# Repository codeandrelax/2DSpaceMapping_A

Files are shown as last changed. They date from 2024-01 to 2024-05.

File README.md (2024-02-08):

# O projektu 🚗
Specifikacija projektnog zadatka od strane project owner-a (uopšteni zahtjevi):

- autonomno vozilo
- upravljačka ploča (MCU: PIC24FJ64GAxx)
- lidar
- aplikacija

Cilj projektnog zadatka jeste realizacija autonomnog vozila koje ima mogućnost kretanja kroz prostoriju i mapiranje područja oko njega. Vozilo se sastoji od šasije sa 4 točka (2 slobodna točka i 2 točka pogonjena na DC motor) kojima upravlja upravljačka ploča bazirana na mikrokontroleru PIC24FJ64GA.

Kao ključni element same ploče, koristimo mikrokontroler iz familije PIC24FJ64GA za upravljanje i kontrolu sistema. Za komunikaciju sa već postojećom pločom koristimo I2C, a za komunikaciju sa drugim periferijama koristimo UART i SPI. Jedan od glavnih zahtjeva korisnika jeste da se ostvari bežična komunikacija i daljinsko upravljanje samog vozila, za šta je neophodno koristiti WiFi modul koji povezujemo putem UART interfejsa sa mikrokontrolerom. Mapiranje prostora i kontrola kretanja se vrši uz pomoć Lidara. Korisnik može kontrolisati kretanje vozila pomoću korisničke aplikacije i njenog GUI-a dok prati pogled na prostor u realnom vremenu. Na kraju, neophodno je razviti PC aolikaciju za prikaz reljefa oko samog vozila. Minimalni uslovi koji moraju biti ispunjeni su mogućnost pokretanja i zaustavljanja vozila.
Nakon prvog sastanka sa project owner-om, dobili smo detaljnije specifikacije samog projektnog zadatka koje podrazumijevaju sljedeće:

- PCB pločica može da bude jednoslojna ili dvoslojna
- prilikom izrade PCB ploče koristimo SMD komponente, gdje je to moguće
- minimalna širina veze prilikom rutiranja iznosi 0.254 mm
- nije potrebno projektovati dodatno napajanje, dovoljno je koristiti već postojeće
- budžet za narudzbu i kupovinu komponenata ne bi trebalo da prelazi 30 dolara

Početna šema, neophodna za izradu i projektovanje štampane ploče prikazana je na slici ispod, a detaljnije objašnjenje same šeme i načina spajanja iste nalazi se na Wiki stranici.



Nakon projektovane šema, kao rezultat dobijamo PCB i rutiranu pločicu, prikzanu na slici ispod :



Dostavljamo i 3D model PCB-a :



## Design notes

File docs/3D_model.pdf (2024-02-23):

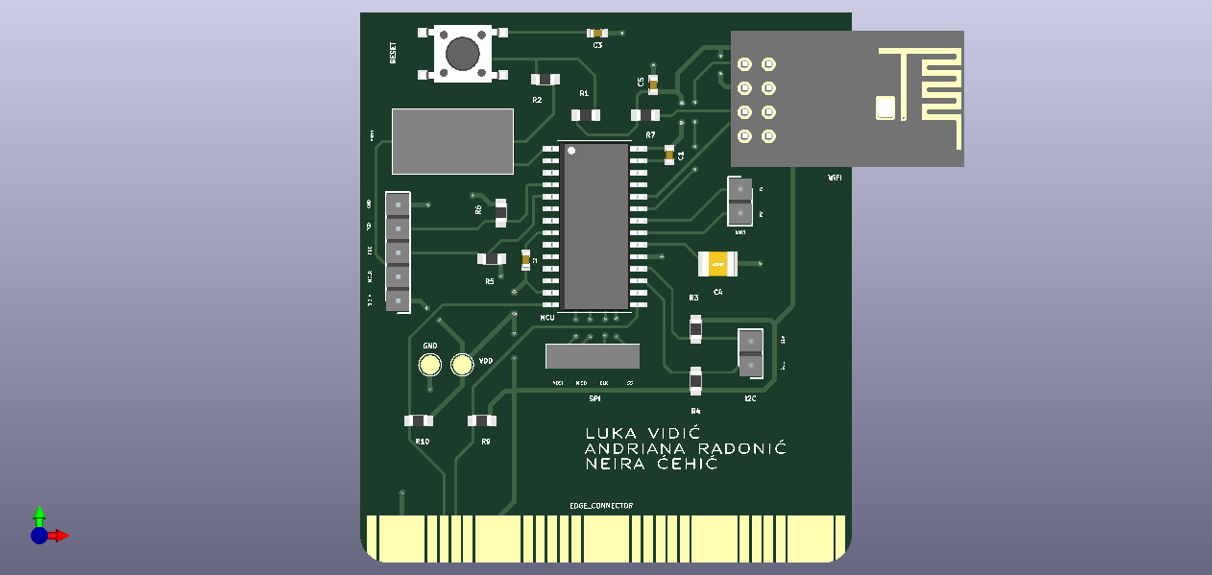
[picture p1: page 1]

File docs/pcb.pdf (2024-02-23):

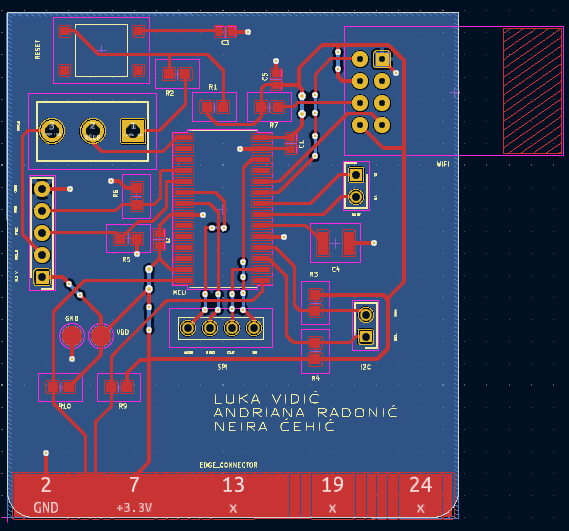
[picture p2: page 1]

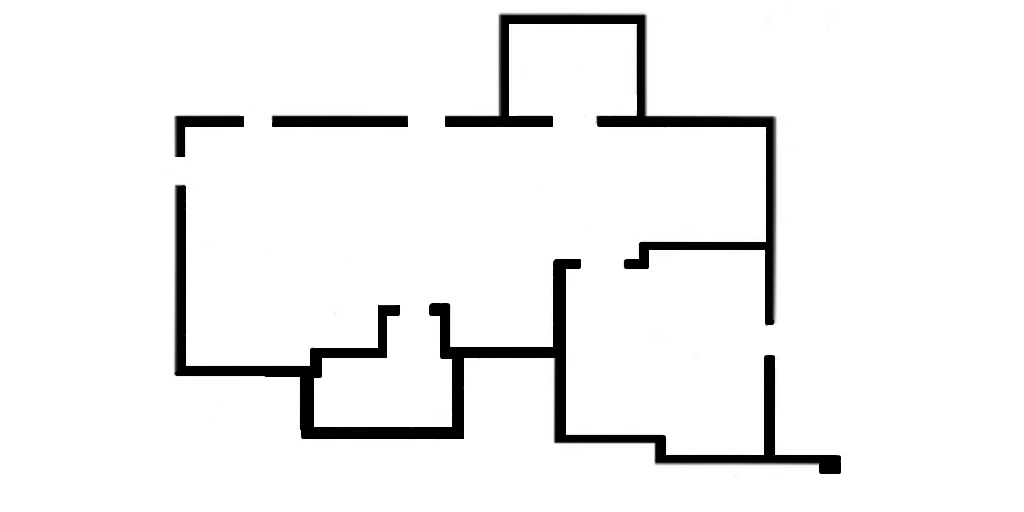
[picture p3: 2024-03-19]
software/lidar_simulator/map.png

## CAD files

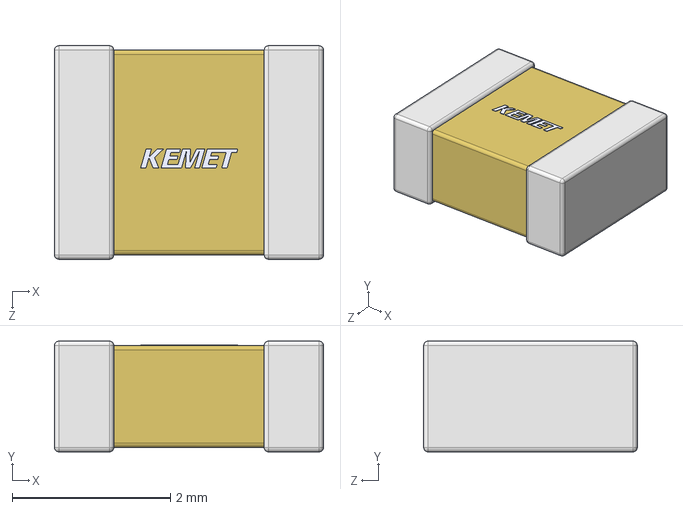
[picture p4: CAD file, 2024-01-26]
kicad/sema_i_pcb/models/CAPACITORS_RESISTORS/10uF.stp
3.40 x 1.40 x 2.70 mm

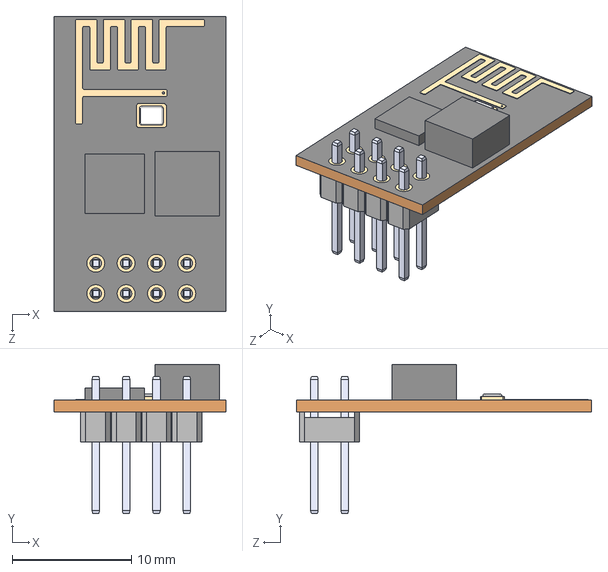
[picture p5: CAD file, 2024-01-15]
kicad/sema_i_pcb/models/ESP8266/ESP8266-01_ESP-01.step
14.4 x 12.5 x 24.7 mm

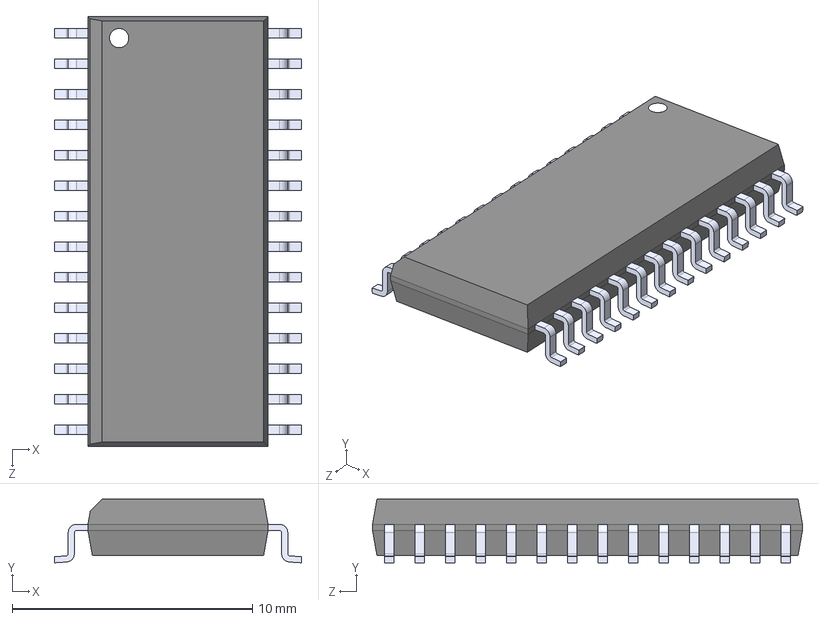
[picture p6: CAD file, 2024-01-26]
kicad/sema_i_pcb/models/MCU/PIC24FJ64GA002-I_SO.STEP
10.3 x 2.65 x 17.9 mm

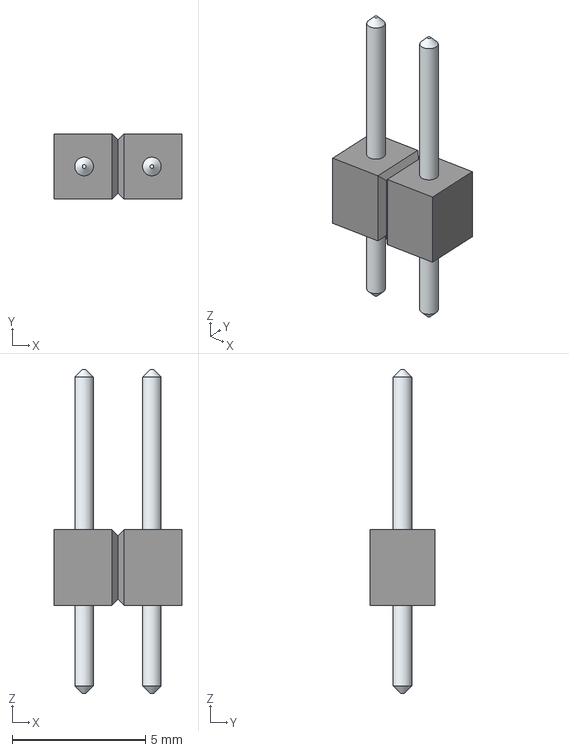
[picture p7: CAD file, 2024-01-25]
kicad/sema_i_pcb/models/PIN_HEADERS/A2-2PA-2.54DSA_71_.stp
4.78 x 2.44 x 12.1 mm
LeadsArray

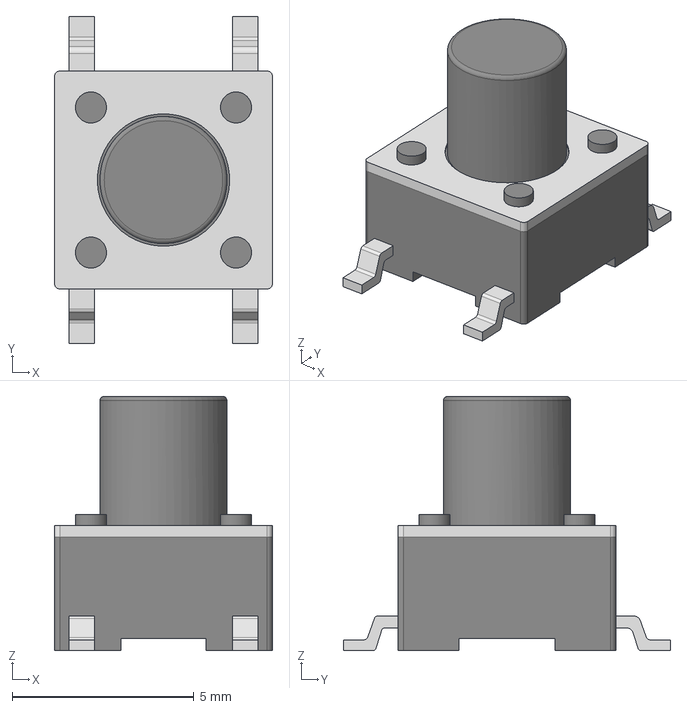
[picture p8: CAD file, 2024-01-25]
kicad/sema_i_pcb/models/PUSH_BUTTON/COM-12992.stp
6.00 x 9.00 x 7.00 mm

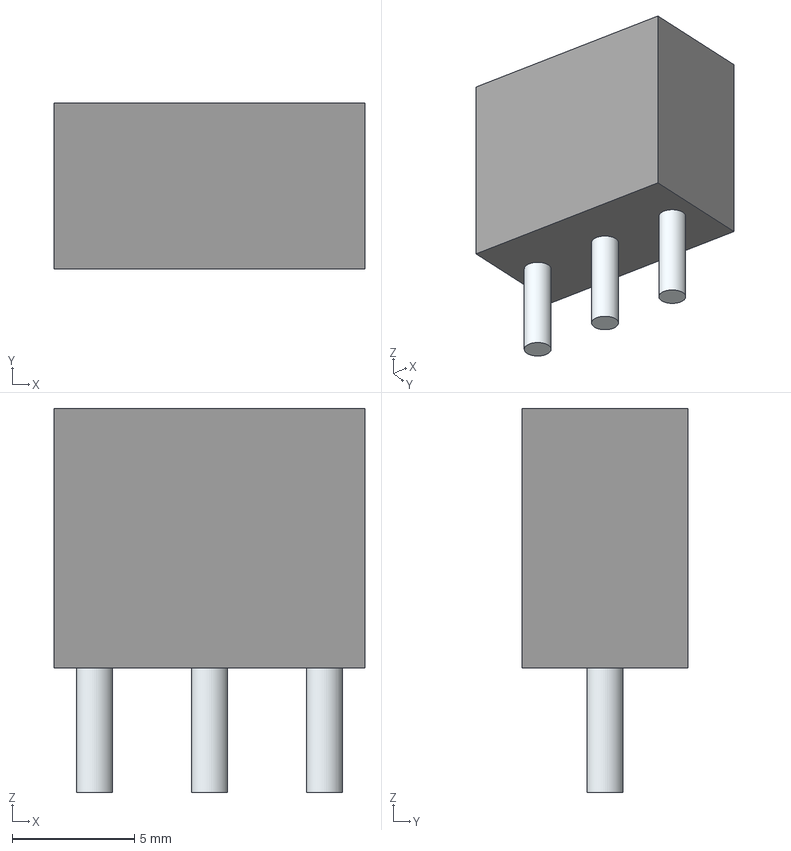
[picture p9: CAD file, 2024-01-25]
kicad/sema_i_pcb/models/SPDT_SWITCH/SLW-1276864-4A-D.stp
12.7 x 6.80 x 15.7 mm
Leads

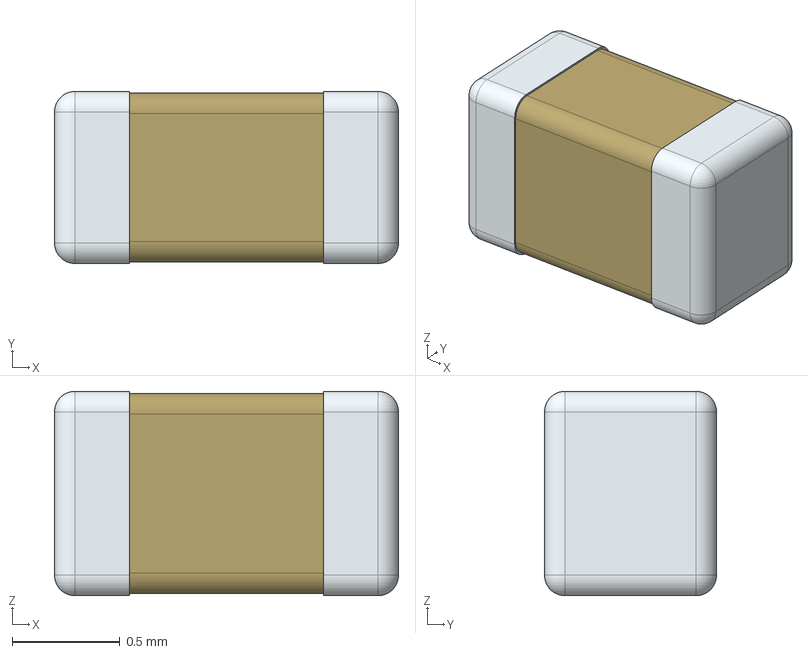
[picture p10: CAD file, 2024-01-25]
kicad/sema_i_pcb/models/CAPACITORS_RESISTORS/100nF.stp
1.60 x 0.8 x 0.95 mm

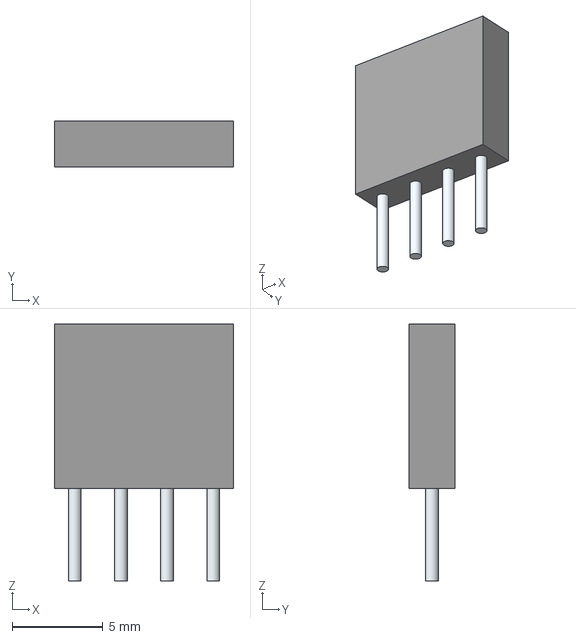
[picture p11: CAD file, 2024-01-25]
kicad/sema_i_pcb/models/PIN_HEADERS/A2-4PA-2.54DSA_71_.stp
9.86 x 2.54 x 14.1 mm
Leads x 4

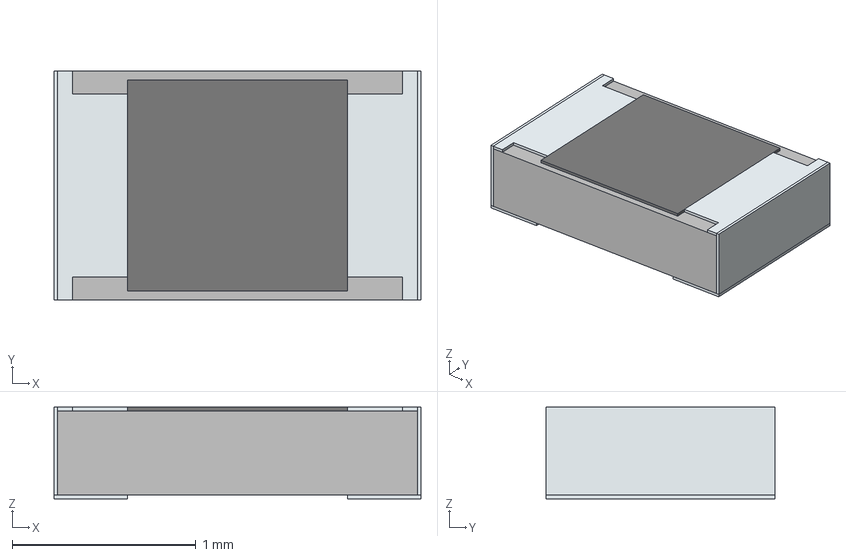
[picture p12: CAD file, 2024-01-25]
kicad/sema_i_pcb/models/CAPACITORS_RESISTORS/4k7.stp
2.00 x 1.25 x 0.5 mm
solidBody
solidTop
solidTerminal1
solidTerminal2
solidTerminal3

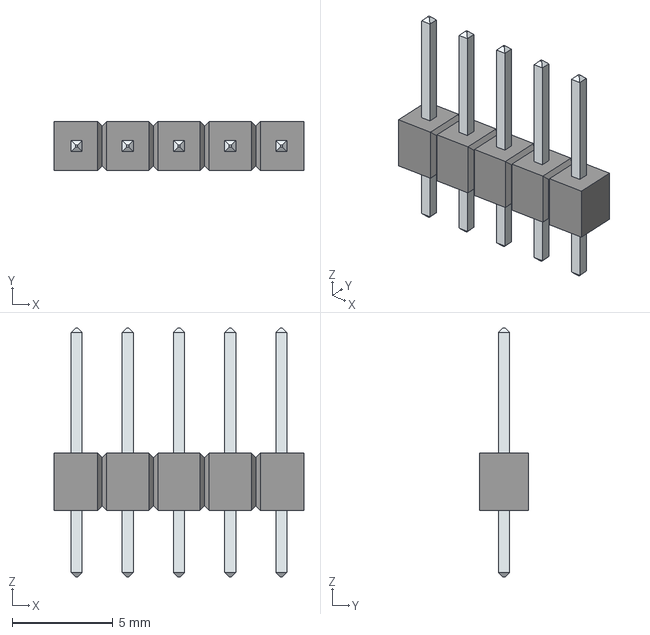
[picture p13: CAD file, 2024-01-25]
kicad/sema_i_pcb/models/PIN_HEADERS/A2-5PA-2.54DSA_71_.stp
12.4 x 2.44 x 12.3 mm
LeadsArray

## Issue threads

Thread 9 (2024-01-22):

Kreiranje simbola i modela za Edge Connector

lukavidic, 2024-01-22:
Zadatak je kreirati simbol i PCB layout komponente _Edge Connector_ u alatu KiCad koja je neophodna za komunikaciju mikrokontrolera sa postojećom štampanom pločom. Rezultat izvršavanja ovog zadatka je gotov model koji je iskorišćen u glavnoj šemi kao i wiki stranica koja opisuje _Edge Connector_.

lukavidic, 2024-01-23:
Težina zadatka: 8

Neira7, 2024-01-23:
Težina zadatka: 9

RadonicA, 2024-01-23:
Težina zadatka : 9

RadonicA, 2024-01-23:
Na ovaj zadatak utroseno je 3h 15m.

RadonicA, 2024-01-25:
Procijenjeno vrijeme izrade: 6h

lukavidic, 2024-01-25:
Utroseno vrijeme za izradu zadatka: ~ 6h 30min

Closed 2024-01-25.

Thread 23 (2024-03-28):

Upoznavanje sa servo motorom

RadonicA, 2024-03-28:
Upoznati se sa karakteristikama i funkcijama samog servo motora. Napraviti wiki stranicu sa detaljnijim opisom.

Neira7, 2024-04-02:
Tezina zadatka: 5

lukavidic, 2024-04-02:
Težina zadatka: 3

lukavidic, 2024-04-02:
Procjenjeno vrijeme izrade: 3h

lukavidic, 2024-04-02:
Utrošeno vrijeme za izradu: ~10h

Closed 2024-04-05.

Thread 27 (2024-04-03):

Integracija servo motora i IR senzora

lukavidic, 2024-04-03:
Napisati firmware program koji integriše funkcionalnosti servo motora i IR senzora tako da se dobije radar koji će da skenira okruženja autonomnog vozila.

lukavidic, 2024-04-03:
Procjenjeno vrijeme rada: 2h

lukavidic, 2024-04-03:
Težina zadatka: 7

RadonicA, 2024-04-03:
Težina zadatka: 7

Neira7, 2024-04-04:
Težina zadatka: 7

lukavidic, 2024-04-15:
Utrošeno vrijeme za izradu: ~20h

Closed 2024-04-15.

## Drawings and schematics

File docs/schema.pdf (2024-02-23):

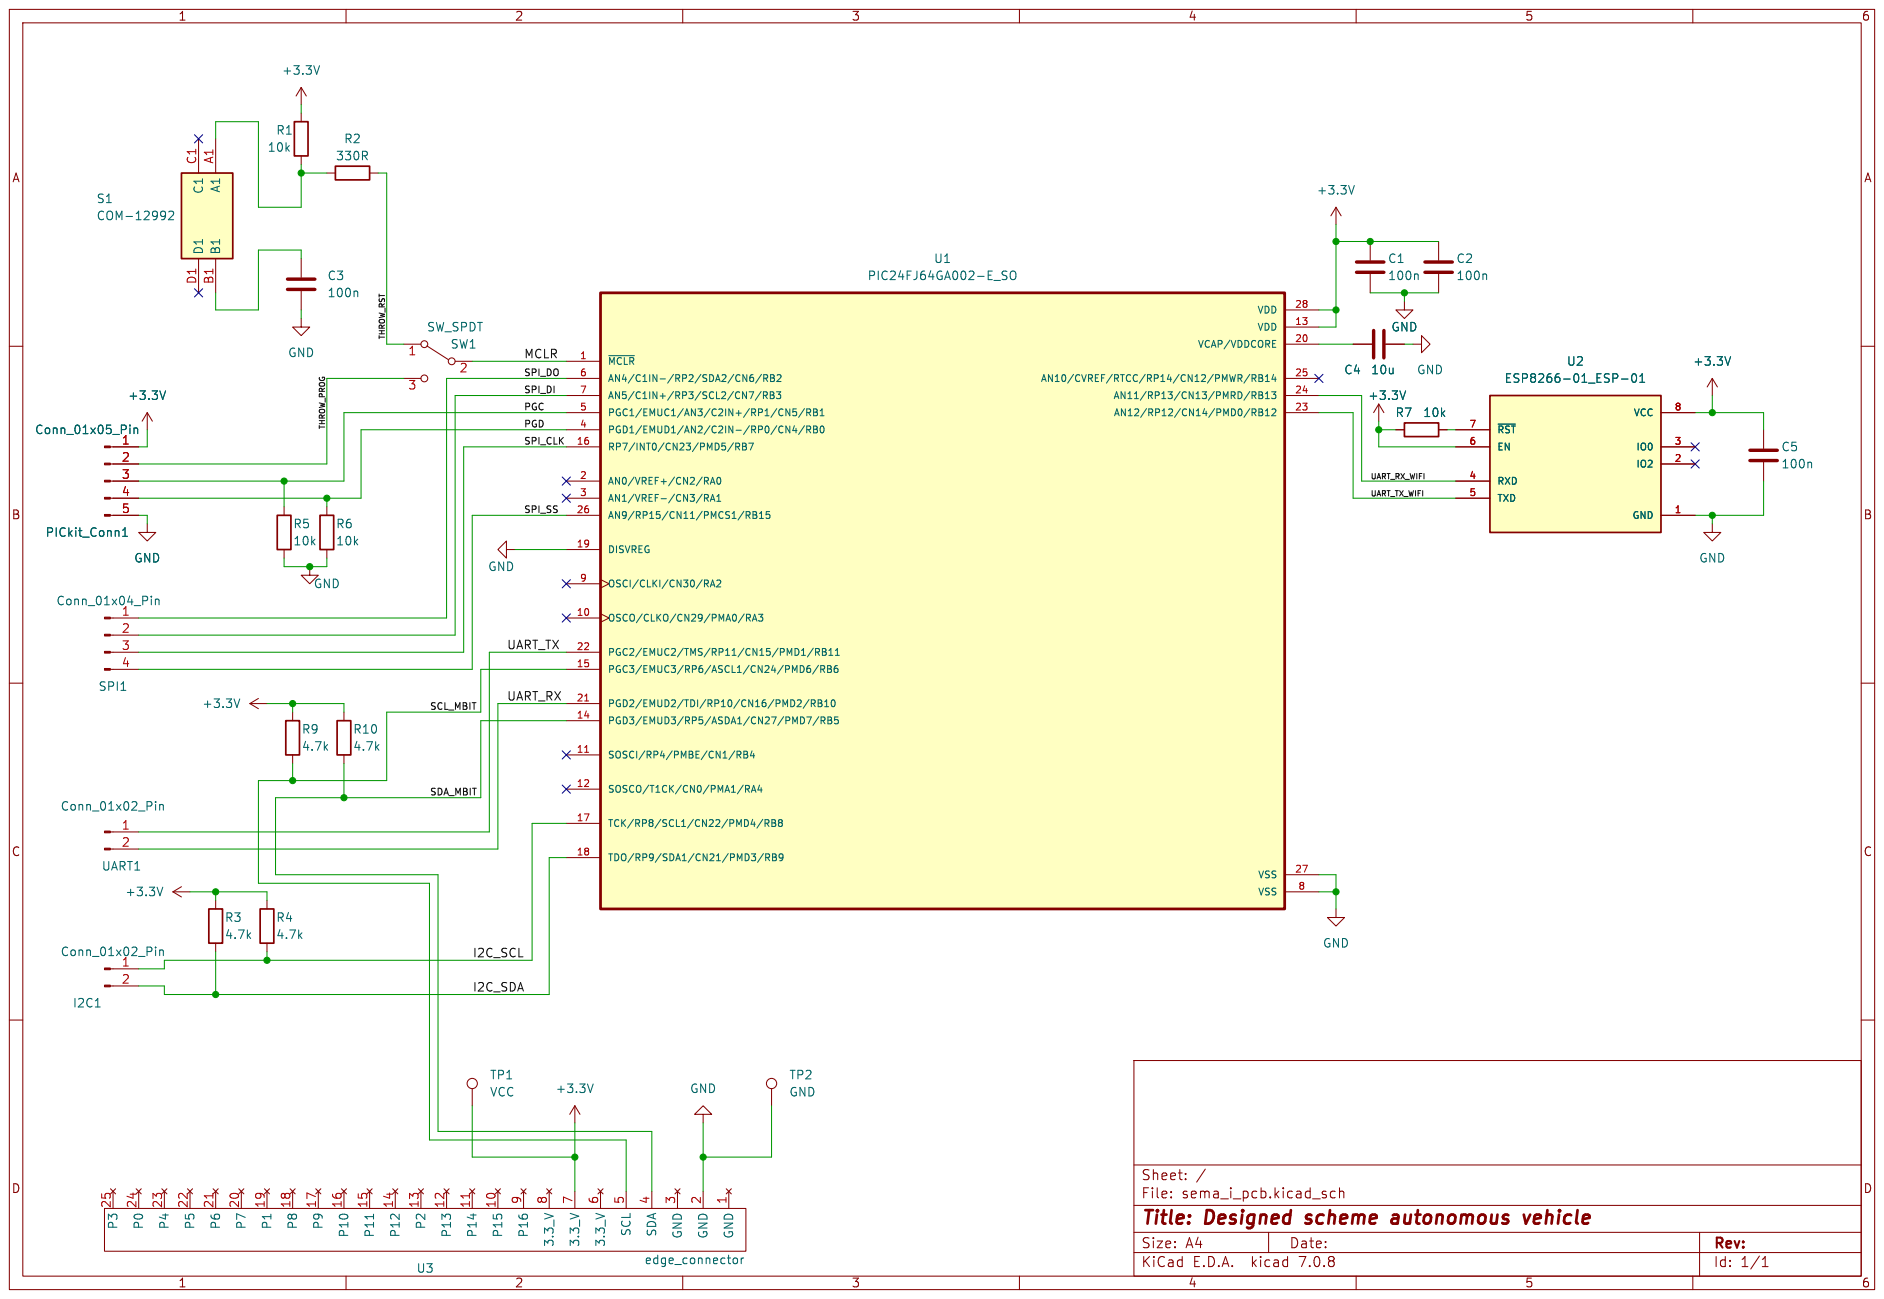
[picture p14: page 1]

Id: 1/1 Title: Designed scheme autonomous vehicle

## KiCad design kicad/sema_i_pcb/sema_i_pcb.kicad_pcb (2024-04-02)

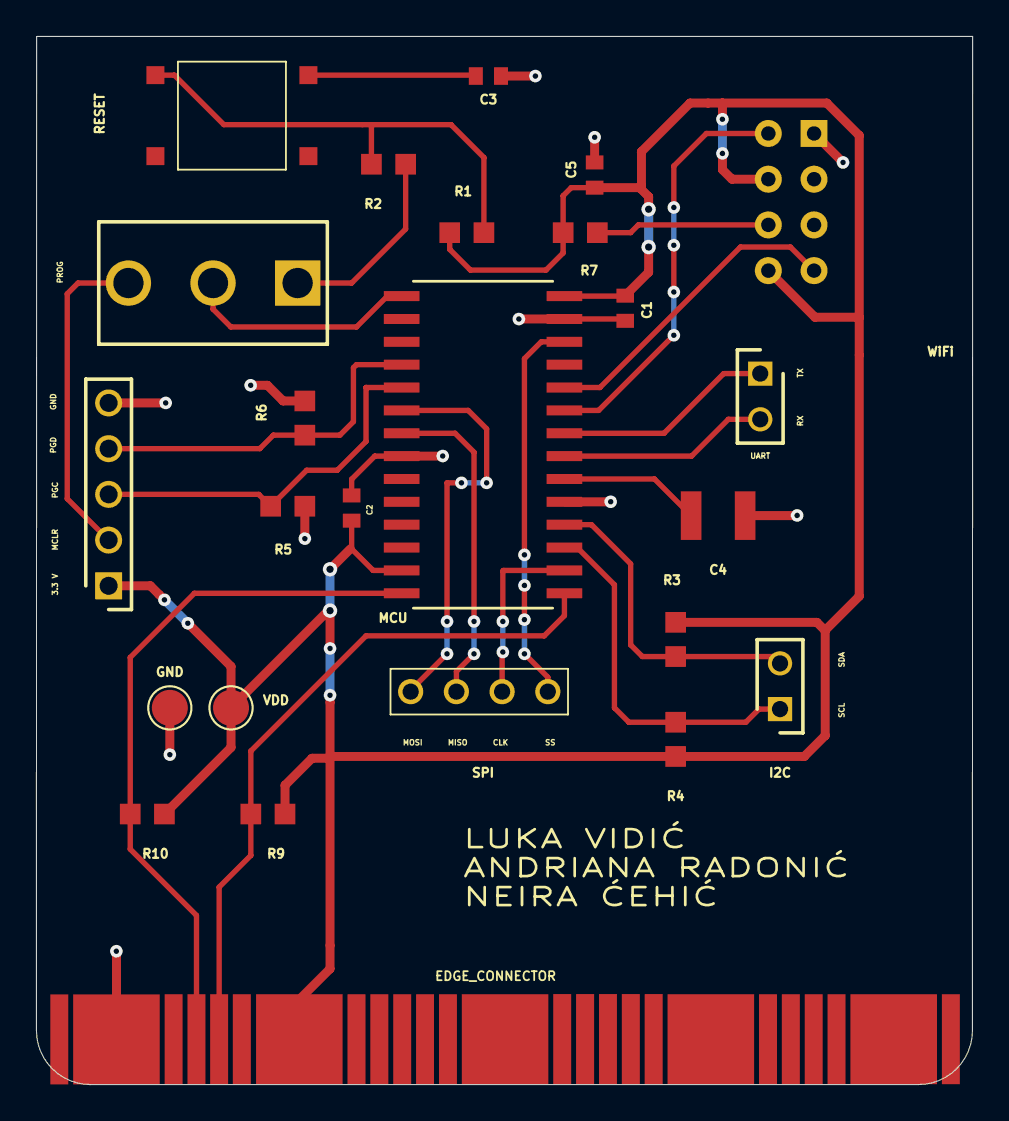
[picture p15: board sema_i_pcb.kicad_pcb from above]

Board: 2 copper layers, 52.0 x 58.2 mm, 25 parts (0 on the bottom side), 23 nets.

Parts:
C1, C2, C3, C5: 100n; 100nF
C4: 10u; 10uF
EDGE_CONNECTOR: edge_connector
GND: GND; TestPoint_Pad_D2.0mm
I2C: Conn_01x02_Pin; HDRV2W70P0X254_1X2_478X244X884P
MCU: PIC24FJ64GA002-E_SO; SOIC28-W_MC_MCH
PICkit_Conn1: Conn_01x05_Pin; HDRV5W56P0X254_1X5_1240X244X904P
PROG: SW_SPDT; SLW12768644AD
R1, R5, R6, R7: ERA6AEB1020V; 10k
R2: ERA6AEB1020V; 330R
R3, R4, R9, R10: 4.7k; 4k7
RESET: COM-12992; COM12992
SPI: Conn_01x04_Pin; A24PA254DSA71
U2: ESP8266-01_ESP-01; XCVR_ESP8266-01_ESP-01
UART: Conn_01x02_Pin; HDRV2W70P0X254_1X2_478X244X884P
VDD: VCC; TestPoint_Pad_D2.0mm

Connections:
+3.3V: C1.1, C2.1, C5.1, EDGE_CONNECTOR.7 (3.3_V), MCU.13 (VDD), MCU.28 (VDD), PICkit_Conn1.1, R1.1, R3.1, R4.1, R7.1, R9.1, R10.1, U2.6 (EN), U2.8 (VCC), VDD.1
/I2C_SCL: I2C.1, MCU.17 (TCK/RP8/SCL1/CN22/PMD4/RB8), R4.2
/I2C_SDA: I2C.2, MCU.18 (TDO/RP9/SDA1/CN21/PMD3/RB9), R3.2
/MCLR: MCU.1 (~MCLR), PROG.2 (B)
/PGC: MCU.5 (PGC1/EMUC1/AN3/C2IN+/RP1/CN5/RB1), PICkit_Conn1.3, R5.1
/PGD: MCU.4 (PGD1/EMUD1/AN2/C2IN-/RP0/CN4/RB0), PICkit_Conn1.4, R6.1
/SCL_MBIT: EDGE_CONNECTOR.5 (SCL), MCU.15 (PGC3/EMUC3/RP6/ASCL1/CN24/PMD6/RB6), R9.2
/SDA_MBIT: EDGE_CONNECTOR.4 (SDA), MCU.14 (PGD3/EMUD3/RP5/ASDA1/CN27/PMD7/RB5), R10.2
/SPI_CLK: MCU.16 (RP7/INT0/CN23/PMD5/RB7), SPI.3
/SPI_DI: MCU.7 (AN5/C1IN+/RP3/SCL2/CN7/RB3), SPI.2
/SPI_DO: MCU.6 (AN4/C1IN-/RP2/SDA2/CN6/RB2), SPI.1
/SPI_SS: MCU.26 (AN9/RP15/CN11/PMCS1/RB15), SPI.4
/THROW_PROG: PICkit_Conn1.2, PROG.3 (C)
/THROW_RST: PROG.1 (A), R2.2
/UART_RX: MCU.21 (PGD2/EMUD2/TDI/RP10/CN16/PMD2/RB10), UART.2
/UART_RX_WIFI: MCU.24 (AN11/RP13/CN13/PMRD/RB13), U2.4 (RXD)
/UART_TX: MCU.22 (PGC2/EMUC2/TMS/RP11/CN15/PMD1/RB11), UART.1
/UART_TX_WIFI: MCU.23 (AN12/RP12/CN14/PMD0/RB12), U2.5 (TXD)
GND: C1.2, C2.2, C3.2, C4.2, C5.2, EDGE_CONNECTOR.2 (GND), GND.1, MCU.8 (VSS), MCU.19 (DISVREG), MCU.27 (VSS), PICkit_Conn1.5, R5.2, R6.2, U2.1 (GND)
unnamed: C3.1, RESET.B1
unnamed: R1.2, R2.1, RESET.A1
unnamed: C4.1, MCU.20 (VCAP/VDDCORE)
unnamed: R7.2, U2.7 (~RST)

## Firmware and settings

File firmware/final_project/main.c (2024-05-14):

#include "hcsr04.h"
#include "movement.h"
#include "esp8266.h"

/* Frekvencija PWM signala za servo motor */
#define PWM_FREQ 50
/* Bitska brzina UART prenosa za ESP8266 */
#define BAUD_RATE 115200
/* Bitska brzina SCL takta I2C prenosa */
#define SCL_RATE 100000
/* Rezolucija radara (broj tacaka u kojima se uzima odmjerak) */
#define RADAR_RESOLUTION 10
/* Velicina bafera za povratne podatke ESP8266 modula */
#define BUFFER_LEN 1024
/* Duzina median filtra koji filtrira senzorske podatke */
#define FILTER_LEN 5
/* Separatorski string za format poruke koja prenosi podatke */
#define SEPARATOR ","
/* Predefinisani znak koji oznacava nastavak kretanja vozila */
#define START_LABEL '%'
/* Predefinisani znak koji oznacava zaustavljanje kretanja vozila */
#define STOP_LABEL '#'
/* Vremenski interval u ms potreban za skretanje vozila */
#define TURN_DELAY 300
/* Vremenski interval u ms potreban da IR senzor uzme novi podatak */
#define SENSOR_DELAY 25
/* Granicna vrijednost distance od prepreke nakon koje se zaustavlja vozilo */
#define DISTANCE_THRESHOLD 30

#define IR_PIN F2
#define SERVO_PIN F7
#define ESP_TX_PIN F13
#define ESP_RX_PIN F14

// Faktor popune PWM signala koji odgovara uglu od priblizno 0 stepeni servo motora
const double SERVO_MIN_DUTY = 2.5;
// Faktor popune PWM signala koji odgovara uglu od priblizno 180 stepeni servo motora
const double SERVO_MAX_DUTY = 12.5;
// Pomak faktora popune koji postavlja servo na uglove 45, 135 stepeni (od max i min)
const double SERVO_OFFSET = 4.5;
// Duzina poruke koja se salje udaljenom racunarskom sistemu
const unsigned MESSAGE_LEN = (RADAR_RESOLUTION + 1) * 10;
// Faktori popune koji se koriste za odredjivanje pravca kretanja
const double DUTY_CYCLES[4] = {SERVO_MIN_DUTY, 
                               SERVO_MIN_DUTY + SERVO_OFFSET,
                               SERVO_MAX_DUTY - SERVO_OFFSET,
                               SERVO_MAX_DUTY};

volatile char buffer[BUFFER_LEN];
volatile unsigned buf_idx = 0;
unsigned start_stop_flag = 0;
unsigned pwm_period = 0;

/**
 * @brief Prekidna rutina koja obradjuje prijem podatka preko UART veze
 */
void UART1_Receiver_Interrupt() iv 0x00002A
{
  IEC0.U1RXIE = 0;
  buffer[buf_idx] = UART1_Read();
  if(buffer[buf_idx] == START_LABEL)
  {
    start_stop_flag = 1;
  }
  else if(buffer[buf_idx] == STOP_LABEL)
  {
    start_stop_flag = 0;
  }
  buf_idx++;
  IEC0.U1RXIE = 1;
  IFS0.U1RXIF = 0;
}

/**
 * @brief Prekidna rutina koja obradjuje gresku preteka UART bafera za podatke
 */
void UART1_Error_Interrupt() iv 0x000096
{
  IEC4.U1ERIE = 0;
  U1STA.OERR  = 0;
  IEC4.U1ERIE = 1;
  IFS4.U1ERIF = 0;
}

/**
 * @brief Funkcija provjerava odgovor ESP8266 modula na prethodno datu komandu
 * @returns 1 - odgovor je OK, -1 - odgovor je ERROR, 0 - nema odgovora
 */
short check_response()
{
  if(strstr(buffer, MESSAGE_OK) != 0)
  {
    return 1;
  }
  else if(strstr(buffer, MESSAGE_ERROR) != 0)
  {
    return -1;
  }
  else
  {
    return 0;
  }
}

/**
 * @brief Funkcija koja ceka polling metodom na odgovor ESP8266 modula
 * @returns Krajnji dobijeni odgovor
 */
short poll_response()
{
  short response = 0;
  do
  {
    response = check_response();
    Delay_ms(100);
  }while(response == 0);
  memset(buffer, 0, BUFFER_LEN);
  buf_idx = 0;
  return response;
}

/**
 * @brief Funkcija koja uspostavlja povezivanje na WiFi mrezu
 */
void establish_wifi_connection()
{
  // Prvo resetujemo modul
  UART1_Write_Text(CMD_RST);
  Delay_ms(3000);
  memset(buffer, 0, BUFFER_LEN);
  buf_idx = 0;
  // Podesimo STATION rezim rada
  UART1_Write_Text(CMD_STA_MODE);
  poll_response();
  // Podesimo jednokanalnu komunikaciju
  UART1_Write_Text(CMD_SINGLE_CONN_TYPE);
  poll_response();
  // Povezemo se na WiFi mrezu
  UART1_Write_Text(CMD_WIFI_CONN);
  poll_response();
}

/**
 * @brief Funkcija koja salje poruku udaljenom racunarskom sistemu
 * preko WiFi mreze putem ESP8266 modula
 * @param[in] message Poruka koju treba poslati
 */
void send_wifi_message(char* message)
{
  char cmd[32];
  sprintf(cmd, CMD_SEND, strlen(message));
  UART1_Write_Text(cmd);
  poll_response();
  UART1_Write_Text(message);
}

/**
 * @brief Funkcija koja implementira median filtar, radi izbjegavanja
 * ocitavanja suma sa senzora.
 * @param[in] array Niz podataka sa senzora koji se filtrira
 */
unsigned median_filter(unsigned array[])
{
  unsigned i,j;
  unsigned swap;
  for(i=0; i<FILTER_LEN; i++)
  {
    for(j=0; j<FILTER_LEN; j++)
    {
      if(array[i] > array[j])
      {
        swap = array[i];
        array[i] = array[j];
        array[j] = swap;
      }
    }
  }
  return array[FILTER_LEN/2];
}

/**
 * @brief Funkcija koja odlucuje pravac kretanja nakon
 * @details Povratna vrijednost oznacava potrebni pravac kretanja:
 *          0 - Ostro skretanje u lijevo
 *          1 - Blago skretanje u lijevo
 *          2 - Blago skretanje u desno
 *          3 - Ostro skretanje u desno
 * @returns Pravac kretanja dat kao cijeli broj opisan u sekciji details
 */
unsigned decide_direction()
{
  unsigned direction = 4;
  unsigned min_distance = 1024;
  unsigned distances[FILTER_LEN];
  unsigned dist_tmp = 0;
  unsigned i,j;
  for(i=0; i<4; i++)
  {
    PWM_Set_Duty(DUTY_CYCLES[i] * pwm_period / 100, 1);
    Delay_ms(150);
    for(j=0; j<FILTER_LEN; j++)
    {
      distances[j] = ADC1_Get_Sample(4);
      Delay_ms(SENSOR_DELAY);
    }
    dist_tmp = median_filter(distances);
    if(dist_tmp < min_distance)
    {
      min_distance = dist_tmp;
      direction = i;
    }
  }
  return direction;
}

void main()
{
  unsigned i = 0, j = 0;
  unsigned distances[FILTER_LEN];
  unsigned adc_value = 0.0;
  unsigned obstacle_detected = 0;
  short resp = 0;
  double duty_cycle = SERVO_MIN_DUTY;
  double duty_increment = (SERVO_MAX_DUTY - SERVO_MIN_DUTY) / RADAR_RESOLUTION;
  char distance_str[6];
  char angle_str[15];
  char message[MESSAGE_LEN];

  // Konfiguracija internih registara pinova MCU-a
  CLKDIV = 0;
  AD1PCFGL = 0xFFEF; // Podesi pin IR senzora kao analogni, ostatak digitalni
  TRISB = 0;
  LATB = 0;
  TRISB.IR_PIN = 1; // Podesi pin IR senzora kao ulazni
  TRISB.ESP_RX_PIN = 1; // Podesi RX pin UART veze kao ulazni
  ODCB.SERVO_PIN = 1; // Podesi servo pin kao open-drain za 5V PWM izlaz
  RPOR3 = 0x1200; // Remapiraj servo pin kao OC1 za omogucenje PWM-a
  RPOR6 = 0x0300; // Remapiraj pin za UART TX kao U1TX
  RPINR18 = 0x1F0E; // Remapiraj UART RX pin kao U1RX

  // Konfiguracija registara za prekide
  IPC2bits.U1RXIP = 5;
  IFS0.U1RXIF = 0;
  IEC0.U1RXIE = 1;
  IPC16bits.U1ERIP = 5;
  IFS4.U1ERIF = 0;
  IEC4.U1ERIE = 1;

  // Inicijalizuj A/D konvertor
  ADC1_Init();

  // Inicijalizuj PWM
  pwm_period = PWM_Init(PWM_FREQ, 1, 8, 2);
  PWM_Start(1);

  // Inicijalizuj UART
  UART1_Init(BAUD_RATE);
  
  // Inicijalizacija softverskog I2C protokola
  I2C1_Init(SCL_RATE);

  // Inicijalizuj HC-SR04
  HCSR04_Init();

  Delay_ms(100);
  
  init_driving();

  establish_wifi_connection();

  // Uspostavimo TCP vezu sa udaljenom aplikacijom
  UART1_Write_Text(CMD_START_TCP);
  resp = poll_response();

  memset(buffer, 0, BUFFER_LEN);
  buf_idx = 0;
  start_stop_flag = 1;

  /**
   * Svaka iteracija while petlje alternirajuce pomjera servo motor od 0 do 180
   * i nazad od 180 do 0 stepeni u koracima odredjenim rezolucijom radara.
   */
  while(1)
  {
    _wait_for_start_:
    if(obstacle_detected == 1)
    {
      drive_stop();
      obstacle_detected = 0;
      switch(decide_direction())
      {
        case 0:
          drive_hard_left();
          break;
        case 1:
          drive_soft_left();
          break;
        case 2:
          drive_soft_right();
          break;
        case 3:
          drive_hard_right();
          break;
        default:
          drive_stop();
        Delay_ms(TURN_DELAY);
      }
    }
    if(start_stop_flag == 1)
    {
      drive_forward();
      memset(distance_str, 0, 6);
      memset(angle_str, 0, 15);
      memset(message, 0, MESSAGE_LEN);
      for(i=0; i<=RADAR_RESOLUTION; i++)
      {
        obstacle_detected = (HCSR04_Get_Distance() <= DISTANCE_THRESHOLD);
        if((start_stop_flag == 0) || (obstacle_detected == 1))
        {
          goto _wait_for_start_;
        }
        PWM_Set_Duty(duty_cycle * pwm_period / 100, 1);
        Delay_ms(60);
        for(j=0; j<FILTER_LEN; j++)
        {
          distances[j] = ADC1_Get_Sample(4);
          Delay_ms(SENSOR_DELAY);
        }
        adc_value = median_filter(distances);
        WordToStr(adc_value, distance_str);
        FloatToStr(duty_cycle, angle_str);
        strncat(message, distance_str, 6);
        strcat(message, SEPARATOR);
        strncat(message, angle_str, 4);
        strcat(message, SEPARATOR);
        duty_cycle += duty_increment;
      }
      obstacle_detected = (HCSR04_Get_Distance() <= DISTANCE_THRESHOLD);
      if((start_stop_flag == 0) || (obstacle_detected == 1))
      {
        goto _wait_for_start_;
      }
      message[strlen(message) - 1] = 0;
      duty_cycle -= duty_increment;
      duty_increment *= (-1.0);
      if(resp == 1)
      {
        send_wifi_message(message);
      }
    }
    else
    {
      duty_cycle = SERVO_MIN_DUTY;
      duty_increment = (SERVO_MAX_DUTY - SERVO_MIN_DUTY) / RADAR_RESOLUTION;
      PWM_Set_Duty(SERVO_MIN_DUTY * pwm_period / 100, 1);
      drive_stop();
    }
  }
}

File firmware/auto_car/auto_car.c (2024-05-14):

/** @file auto_car.c
 *
 * @brief Fajl sa izvornim C kodom koji implementira logiku 
 * kretanja autonomnog vozila. 
 */

#define DEVICE_ADDR 0xE0
#define SERVO_PWM_FREQ 50
#define IR_PIN F2
#define SERVO_PIN F7
#define FILTER_LEN 5

/**
 * Konfiguracija pinova za ostvarenje komunikacije putem
 * softverskog I2C protokola.
 */
sbit Soft_I2C_Sda           at RB9_bit;
sbit Soft_I2C_Scl           at RB8_bit;
sbit Soft_I2C_Sda_Direction at TRISB9_bit;
sbit Soft_I2C_Scl_Direction at TRISB8_bit;

/**
 * Granicna vrijednost koja odredjuje kada treba da se zaustavi
 * vozilo, ako su sve udaljenosti vece od zadate.
 */
const unsigned STOP_THRESHOLD = 250;

/**
 * Niz vrijednost faktora popune PWM signala koji kontrolise rad
 * servo motora. Vrijednosti odgovaraju uglovima od priblizno
 * 0, 45, 90, 135 i 180 stepeni, respektivno.
 */
const float DUTY_CYCLES[5] = {4.0, 5.0, 9.0, 12.0, 14.0};

/*
 * Niz koji cuva udaljenosti dobijene od IR senzora kroz svaku iteraciju
 * od 0 do 180 stepeni zakretanja servo motora
 */
unsigned distances[5] = {0,0,0,0,0};

/**
 * @brief Funkcija koja salje podatak preko I2C protokola
 * @param[in] dev_addr Adresa uredjaja kome se salje podatak
 * @param[in] reg_addr Adresa registra uredjaja u koji se podatak upisuje
 * @param[in] data_value Jednobajtni podatak koji se salje
 */
void I2C_Send_Message(unsigned short dev_addr, unsigned short reg_addr, unsigned short data_value)
{
  Soft_I2C_Start();
  Soft_I2C_Write(dev_addr);
  Soft_I2C_Write(reg_addr);
  Soft_I2C_Write(data_value);
  Soft_I2C_Stop();
}

/**
 * Upis vrijednosti u registre 0x02 - 0x05 upravlja vrijednostima
 * PWM kanala. Vrijednosti u tim registrima podesavaju pravac
 * kretanja autonomnog vozila.
 */
 
/**
 * @brief Funkcija koja podesava vrijednosti registara PWM kanala
 * tako da se obezbjedi kretanje vozila unaprijed.
 */
void drive_forward()
{
  I2C_Send_Message(DEVICE_ADDR, 0x02, 0);
  I2C_Send_Message(DEVICE_ADDR, 0x03, 90);
  I2C_Send_Message(DEVICE_ADDR, 0x04, 0);
  I2C_Send_Message(DEVICE_ADDR, 0x05, 90);
}

/**
 * @brief Funkcija koja podesava vrijednosti registara PWM kanala
 * tako da se obezbjedi blago skretanje vozila ulijevo.
 */
void drive_soft_left()
{
  I2C_Send_Message(DEVICE_ADDR, 0x02, 0);
  I2C_Send_Message(DEVICE_ADDR, 0x03, 80);
  I2C_Send_Message(DEVICE_ADDR, 0x04, 0);
  I2C_Send_Message(DEVICE_ADDR, 0x05, 110);
}

/**
 * @brief Funkcija koja podesava vrijednosti registara PWM kanala
 * tako da se obezbjedi blago skretanje vozila udesno.
 */
void drive_soft_right()
{
  I2C_Send_Message(DEVICE_ADDR, 0x02, 0);
  I2C_Send_Message(DEVICE_ADDR, 0x03, 110);
  I2C_Send_Message(DEVICE_ADDR, 0x04, 0);
  I2C_Send_Message(DEVICE_ADDR, 0x05, 80);
}

/**
 * @brief Funkcija koja podesava vrijednosti registara PWM kanala
 * tako da se obezbjedi naglo skretanje vozila ulijevo.
 */
void drive_hard_left()
{
  I2C_Send_Message(DEVICE_ADDR, 0x02, 0);
  I2C_Send_Message(DEVICE_ADDR, 0x03, 0);
  I2C_Send_Message(DEVICE_ADDR, 0x04, 0);
  I2C_Send_Message(DEVICE_ADDR, 0x05, 255);
}

/**
 * @brief Funkcija koja podesava vrijednosti registara PWM kanala
 * tako da se obezbjedi naglo skretanje vozila udesno.
 */
void drive_hard_right()
{
  I2C_Send_Message(DEVICE_ADDR, 0x02, 0);
  I2C_Send_Message(DEVICE_ADDR, 0x03, 255);
  I2C_Send_Message(DEVICE_ADDR, 0x04, 0);
  I2C_Send_Message(DEVICE_ADDR, 0x05, 0);
}

/**
 * @brief Funkcija koja podesava vrijednosti registara PWM kanala
 * tako da se obezbjedi zaustavljanje vozila.
 */
void drive_stop()
{
  I2C_Send_Message(DEVICE_ADDR, 0x02, 0);
  I2C_Send_Message(DEVICE_ADDR, 0x03, 0);
  I2C_Send_Message(DEVICE_ADDR, 0x04, 0);
  I2C_Send_Message(DEVICE_ADDR, 0x05, 0);
}

/**
 * @brief Funkcija koja odlucuje naredni pravac kretanja vozila za
 * trenutno skenirani polukrug prostora i dobijene udaljenosti.
 */
char decide_direction()
{
  unsigned min_distance = distances[2];
  unsigned direction = 2;
  unsigned idx = 0;
  char turn = 0;
  for(idx=0; idx<5; idx++)
  {
    if((idx % 4 == 0))
    {
      if((distances[idx] + 75) < min_distance)
      {
        direction = idx;
        min_distance = distances[idx];
      }
    }
    else
    {
      if((distances[idx] + 25) < min_distance)
      {
        direction = idx;
        min_distance = distances[idx];
      }
    }
  }
  if(min_distance >= STOP_THRESHOLD)
  {
    drive_stop();
    //UART1_Write_Text("Stopping !\r\n");
    return turn;
  }
  switch(direction)
  {
    case 0:
      drive_hard_left();
      turn = 1;
      //UART1_Write_Text("Turning hard left.\r\n");
      break;
    case 1:
      drive_soft_left();
      //UART1_Write_Text("Turning soft left.\r\n");
      break;
    case 3:
      drive_soft_right();
      //UART1_Write_Text("Turning soft right.\r\n");
      break;
    case 4:
      drive_hard_right();
      turn = 1;
      //UART1_Write_Text("Turning hard right.\r\n");
      break;
    default:
      drive_forward();
      //UART1_Write_Text("Moving forward.\r\n");
  }
  return turn;
}

/**
 * @brief Funkcija koja implementira median filtar, radi izbjegavanja
 * ocitavanja suma sa senzora.
 * @param[in] array Niz podataka sa senzora koji se filtrira
 */
unsigned median_filter(unsigned array[])
{
  unsigned i,j;
  unsigned swap;
  for(i=0; i<FILTER_LEN; i++)
  {
    for(j=0; j<FILTER_LEN; j++)
    {
      if(array[i] > array[j])
      {
        swap = array[i];
        array[i] = array[j];
        array[j] = swap;
      }
    }
  }
  return array[FILTER_LEN/2];
}
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

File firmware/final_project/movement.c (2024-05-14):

/** @file movement.c
 * 
 * @brief Fajl sa izvornim kodom koji implementira funkcije za kontrolu
 * kretanja autonomnog vozila.
*/

#include "movement.h"

/**
 * @brief Funkcija koja salje podatak PWM kontroleru preko I2C protokola
 * @param[in] reg_addr Adresa registra uredjaja u koji se podatak upisuje
 * @param[in] data_value Jednobajtni podatak koji se salje
 */
void I2C_Send_Message(unsigned short reg_addr, unsigned short data_value)
{
  I2C1_Start();
  I2C1_Write(DEVICE_ADDRESS);
  I2C1_Write(reg_addr);
  I2C1_Write(data_value);
  I2C1_Stop();
}

/**
 * @brief Funkcija koja inicijalizuje PWM kontroler za I2C
 * komunikaciju.
 */
void init_driving()
{
  I2C_Send_Message(0x00, 0x01);
  I2C_Send_Message(0xE8, 0xAA);
}

/**
 * Upis vrijednosti u registre 0x02 - 0x05 upravlja vrijednostima
 * PWM kanala. Vrijednosti u tim registrima podesavaju pravac
 * kretanja autonomnog vozila.
 */
 
/**
 * @brief Funkcija koja podesava vrijednosti registara PWM kanala
 * tako da se obezbjedi kretanje vozila unaprijed.
 */
void drive_forward()
{
  I2C_Send_Message(0x02, PWM_MIN_VAL);
  I2C_Send_Message(0x03, PWM_FORWARD_VAL);
  I2C_Send_Message(0x04, PWM_MIN_VAL);
  I2C_Send_Message(0x05, PWM_FORWARD_VAL);
}

/**
 * @brief Funkcija koja podesava vrijednosti registara PWM kanala
 * tako da se obezbjedi blago skretanje vozila ulijevo.
 */
void drive_soft_left()
{
  I2C_Send_Message(0x02, PWM_MIN_VAL);
  I2C_Send_Message(0x03, PWM_MIN_VAL);
  I2C_Send_Message(0x04, PWM_MIN_VAL);
  I2C_Send_Message(0x05, PWM_MAX_VAL - PWM_TURN_OFFSET);
}

/**
 * @brief Funkcija koja podesava vrijednosti registara PWM kanala
 * tako da se obezbjedi blago skretanje vozila udesno.
 */
void drive_soft_right()
{
  I2C_Send_Message(0x02, PWM_MIN_VAL);
  I2C_Send_Message(0x03, PWM_MAX_VAL - PWM_TURN_OFFSET);
  I2C_Send_Message(0x04, PWM_MIN_VAL);
  I2C_Send_Message(0x05, PWM_MIN_VAL);
}

/**
 * @brief Funkcija koja podesava vrijednosti registara PWM kanala
 * tako da se obezbjedi naglo skretanje vozila ulijevo.
 */
void drive_hard_left()
{
  I2C_Send_Message(0x02, PWM_MIN_VAL);
  I2C_Send_Message(0x03, PWM_MIN_VAL);
  I2C_Send_Message(0x04, PWM_MIN_VAL);
  I2C_Send_Message(0x05, PWM_MAX_VAL);
}

/**
 * @brief Funkcija koja podesava vrijednosti registara PWM kanala
 * tako da se obezbjedi naglo skretanje vozila udesno.
 */
void drive_hard_right()
{
  I2C_Send_Message(0x02, PWM_MIN_VAL);
  I2C_Send_Message(0x03, PWM_MAX_VAL);
  I2C_Send_Message(0x04, PWM_MIN_VAL);
  I2C_Send_Message(0x05, PWM_MIN_VAL);
}

/**
 * @brief Funkcija koja podesava vrijednosti registara PWM kanala
 * tako da se obezbjedi zaustavljanje vozila.
 */
void drive_stop()
{
  I2C_Send_Message(0x02, PWM_MIN_VAL);
  I2C_Send_Message(0x03, PWM_MIN_VAL);
  I2C_Send_Message(0x04, PWM_MIN_VAL);
  I2C_Send_Message(0x05, PWM_MIN_VAL);
}

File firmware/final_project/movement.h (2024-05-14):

/** @file movement.h
 * 
 * @brief Heder fajl koji sadrzi konstante i prototipe funkcija koje 
 * opisuju i kontrolisu kretanje autonomnog vozila putem I2C komunikacije 
 * sa drajverskom plocom.
*/

#ifndef _MOVEMENT_H_
#define _MOVEMENT_H_

/* I2C adresa PWM kontrolera drajverske ploce */
#define DEVICE_ADDRESS 0x0E 

/* Maksimalna vrijednost faktora popune drajverskog PWM signala */
#define PWM_MAX_VAL 255 

/* Minimalna vrijednost faktora popune drajverskog PWM signala */
#define PWM_MIN_VAL 0 

/* Brzina kretanja vozila naprijed (data kao faktor popune) */
#define PWM_FORWARD_VAL 90

/* Faktor smanjenja brzine skretanja motora za blaga skretanja */
#define PWM_TURN_OFFSET 75

void init_driving();
void drive_forward();
void drive_soft_left();
void drive_soft_right();
void drive_hard_left();
void drive_hard_right();
void drive_stop();

#endif

/* end of file */

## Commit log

2024-01-15 Issue #4 : Projektovanje elektricne seme
    - Dodana planirana sema
    - Dodani modeli za mikrokontroler i esp8266
    [ESP8266-01_ESP-01.step, PIC24FJ64GA002-I_SP.step, sema_i_pcb.kicad_pcb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]
2024-01-16 Issue #4 : Planiranje projektovanja električne šeme
    - Modifikovani folderi tako da se obezbjedi laksi uvoz modela
    - Modifikovana sema da se omoguci programiranje flash memorije
    - Dodatne izmjene na semi
    [ESP8266-01_ESP-01.step, PIC24FJ64GA002-I_SP.step, sema_i_pcb.kicad_sch]
2024-01-17 Issue #4 : Planiranje projektovanja električne šeme
    - Dodan dio za napajanje, sa DC/DC pretvaračem
    [sema_i_pcb.kicad_sch]
2024-01-18 Issue #4 : Planiranje projektovanja električne šeme
    - Reorganizovana šema i izvršena ERC provjera
    [sema_i_pcb.kicad_sch]
2024-01-22 Issue #4 : Projektovanje električne šeme
    - Uklonjen dio sa DC/DC pretvaračem zbog napajanja sa postojeće ploče
    - Dodan sprežni kondezator između napajanja i mase kod WiFi modula
    - Umjesto jumpera ubačen taster kod kola za reset MCRL pina
    - Dodatne modifikacije i poboljšanja
    [sema_i_pcb.kicad_sch]
2024-01-23 Issue #9 : Kreiranje simbola i modela za Edge Connector Dodan simbol za Edge Connector
2024-01-23 Issue #9 : Kreiranje simbola i modela za Edge Connector Dodan footprint za Edge Connector
2024-01-24 Issue #9 : Kreiranje simbola i modela za Edge Connector
    - Izmjenjen footprint edge connector-a
    [sema_i_pcb.kicad_sch]
2024-01-25 Issue #9 : Kreiranje simbola i modela za Edge Connector
    - Izmjene u footprint-u edge connector-a
2024-01-25 Issue #9 : Kreiranje simbola i modela za Edge Connector
    - Modifikovan footprint edge connector-a
2024-01-25 Issue #3 : Odabir komponenata štampane ploče
    - Odabrane sve potrebne komponente
    - Dodan .csv fajl sa komponentama i linkovima do kataloga
    - Skupljeni svi otisci i modeli potrebni za PCB
    [100nF.stp, 10k.stp, 10uF.stp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]
2024-01-25 Issue #3 : Odabir komponenata štampane ploče
    - Promjenjen odabir za 10k i 4.7k otpornike
    - Ažurirane promjene otisaka i modela u projektu
    [10k.stp, 4k7.stp, komponente.csv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]
2024-01-25 Issue #4 : Projektovanje električne šeme
    - Promjena na šemi, nakon dodatnog čitanja datasheet-a zaključeno je da RST pin WiFi modula mora biti pull-up otpornikom spojen na +3.3V umjesto direktno
    - Novi otpornik dodat u .csv fajl
    [komponente.csv, sema_i_pcb.kicad_sch]
2024-01-26 Issue #7 : Raspored komponenata na PCB
    - Dodana kompletirana šema , spremna za rutiranje.
    [PIC24FJ64GA002-I_SO.STEP, PIC24FJ64GA002-I_SP.step, sema_i_pcb.kicad_pcb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]
2024-01-26 Issue #8 : Rutiranje komponenata na PCB - Dodana rutirana šema
    [sema_i_pcb.kicad_pcb]
2024-01-26 Globalne izmjene:
    - Promjenjena odabrana komponenta 10uF kondenzatora
    - Ažurirani otisak i 3D model novog kondenzatora
    - Popravljene greške u PCB u vezi sa silkscreen-om i zaostalim vezama
    - Izmjene silkscreen-a na drugim otiscima komponenti
    - Blage dorade u dizajnu štampane ploče
    [10uF.stp, sema_i_pcb.kicad_pcb]
2024-01-26 Globalna izmjena:
    - Novoodabrana komponenta 10uF kondenzatora ažurirana u .csv fajlu
    [komponente.csv]
2024-02-23 Update komponente.csv
    Ispravljeni serijski brojevi
    [komponente.csv]
2024-02-23 Issue #11 : Dodavanje dokumentacije
    - Dodana dokumentacija šeme i PCB-a u folder docs
2024-03-19 Issue #16 : Provjeriti mogućnosti implementacije simulatora LIDAR-a
    Dodan izvorni kod koji implementira simulator mobilnog robota sa lidar senzorom koji razmjenjuje mjerne podatke putem WiFi sa glavnim programom
2024-03-19 Issue #16 : Provjeriti mogućnosti implementacije simulatora LIDAR-a
    Obrisani nepotrebni fajlovi
2024-03-19 Issue #12 : Implentacija wireless komunikacije, Issue #14 Implementirati algoritam iscrtavanja
    - dodan izvorni kod koji obuhvata rijesenje navedena dva taska
2024-03-28 Issue #20 : Testiranje i programiranje stampane ploče pomoću programatora
    - Dodan blinky primjer koji testira rad ploče i programiranje
    [blinky.c]
2024-03-28 Issue #20 : Testiranje i programiranje stampane ploče pomoću programatora
    Bug fix
    [blinky.c]
2024-04-02 Issue #24 : Osposobljavanje servo motora
    - Dodan testni firmware kod koji okreće servo motor od 0 do 180 stepeni i nazad kontinualno
    [servo_test.c]
2024-04-02 Issue #22 : Osposobljavanje IR distance click senzora - Dodan kod za provjeru IR distance senzora.
    [komponente.csv, sema_i_pcb.kicad_pcb]
2024-04-15 Issue #27 : Integracija servo motora i IR senzora
    - Dodan incijalni kod za radar koji salje podatke preko UART komunikacije na PC racunar
    [radar.c]
2024-04-17 Issue #26 : Osposobljavanje komunikacije sa postojećom pločom - Dodan kod za testiranje tockova.
    [tockovi_test.c]
2024-04-20 Issue #30 : Integracija i osposobljavanje sistema
    - Dodan kod koji omogućava kretanje vozila kao i detekciju i izbjegavanje prepreka
    [auto_car.c, tockovi_test.c]
2024-04-20 Issue #30 : Integracija i osposobljavanje sistema
    - Dokumentovani svi izvorni fajlovi sa doxygen i obicnim komentarima
    [auto_car.c, blinky.c, ir_distance.c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]
2024-04-25 Issue #30 : Integracija i osposobljavanje sistema
    - Modikovana logika kretanja
    [auto_car.c]
2024-04-25 Issue #25 : Implementacija WiFi komunikacije
    [wifi_module.c]
2024-04-26 Issue #30 : Integracija i osposobljavanje sistema
    - Modifikovana logika kretanja, sada je kretanje dosta bolje
    [auto_car.c]
2024-04-30 Issue #25 : Implementacija WiFi komunikacije
    - Dodan kod koji implementira WiFi komunikaciju putem esp8266 modula
    - Unutar koda je dodatni kod za debagovanje putem UART-USB konvertera
    [wifi_module.c]
2024-05-09 Issue #30 : Integracija i osposobljavanje sistema
    - Integrisane funkcionalnosti radara i WiFi prenosa podataka u svrhu testiranja rada sa aplikacijom za iscrtavanje prostora
    [radar_wifi.c, wifi_module.c]
2024-05-09 Issue #30 : Integracija i osposobljavanje sistema
    - Implementirana funkcionalnost koja testira mogucnost START/STOP detekcije i odgovarajuce akcije
    - Dodatna poboljsanja
    [radar_wifi.c]
2024-05-10 Issue #30 : Integracija i osposobljavanje sistema
    - Popravljeni bagovi koji vode sistem u nestabilno stanje nakon stop-start sekvence
    - Kompletirana integracija radara i WiFi komunikacije
    [radar_wifi.c]
2024-05-11 Issue #33 : Osposobljavanje i testiranje ultrazvučnog senzora
    - Dodan kod biblioteke koja upravlja radom HC-SR04 senzora
    - Dodan izvorni kod glavnog programa koji testira rad biblioteke i senzora tako što dobijene udaljenosti proslijeđuje na UART serijski izlaz
    [hcsr04.c, ultrasonic_sensor.c]
2024-05-14 Issue #30 : Integracija i osposobljavanje sistema
    - Dodane finalne izmjene i pokušaj konačne integracije sistema
    [auto_car.c, hcsr04.c, main.c]
